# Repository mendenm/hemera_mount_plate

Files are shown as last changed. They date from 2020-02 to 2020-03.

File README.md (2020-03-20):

# Hemera Extruder Mounting Plate for Anet A8 - type printers
Designed by Marcus Mendenhall, February, 2020
## Purpose
This project is to develop an very easy-to-use, 3D printable,  adapter plate to mount an [E3D Hemera Extruder](https://e3d-online.com/e3d-hemera) on a 3d printer of the type similar to an Anet A8, Ender 3, or (probably) most Prusa I3-derived printers.

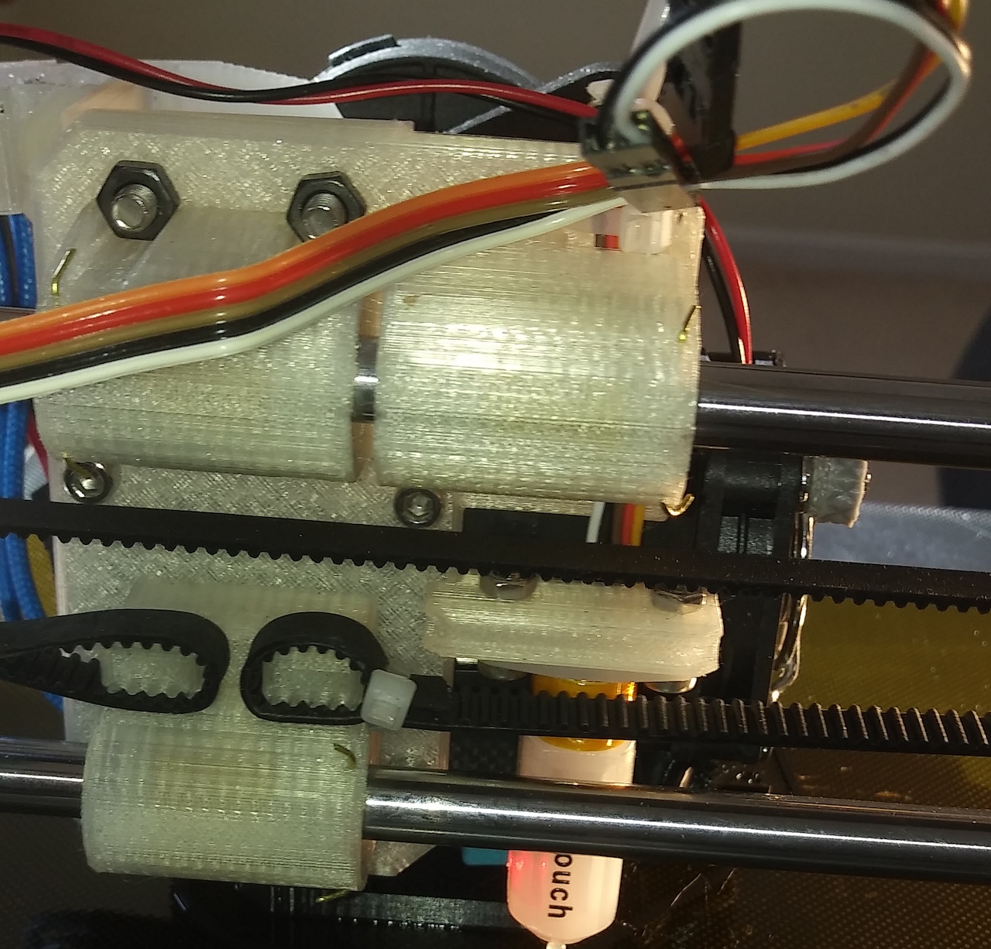
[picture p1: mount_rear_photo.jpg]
Picture of installed mount

Photograph of the back side of the mount, installed with BLTouch.

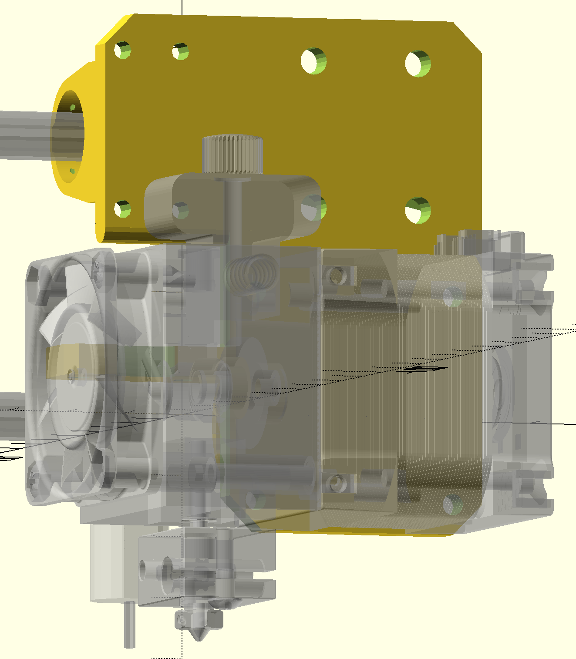
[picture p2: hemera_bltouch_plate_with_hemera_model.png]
Front view of model

Model of the plate in OpenScad showing Hemera and BLTuch ghosted in.  From front.

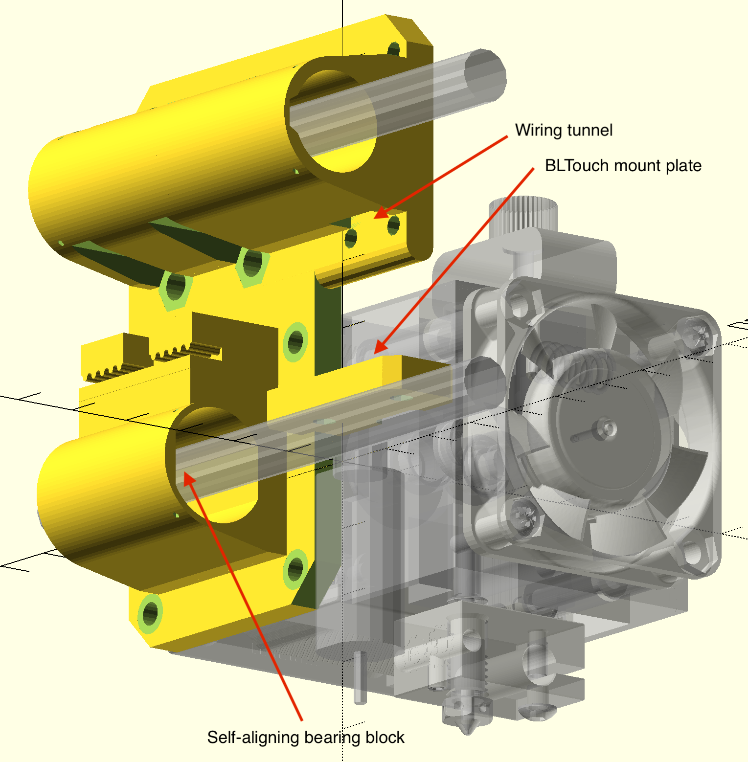
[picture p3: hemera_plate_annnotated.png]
Annotated model view

Annotated image showing some of the features

## Features

The design of plate incorporates a number of critical features. 

1.  The bearing mounting blocks are printed directly onto the plate, greatly reducing the number of screws required to assemble, and the weight.
1. The bottom bearing block is self-aligning.  The design makes it fairly insensitive to the spacing between the guides rods on the printer, and also fairly robust against inaccuracies in the printing itself.  Any rod spacing between 45 mm and 48 mm should work without even modifying the design. This is particularly useful for high-quality, close-fitting bearings such as Igus Drylin, which have little tolerance for misalignment.
1. The design is in [OpenSCAD](https://www.openscad.org), making it very easy to customize.  It is set up with OpenSCAD Customizer-compatible parameters at the top, making simple changes to the design as easy as filling in a dialog box.
1. The plate has an integrated mount for a  [BLTouch bed sensor](https://www.antclabs.com), tightly fit between the Hemera and the guide rods, putting it only 25 mm from the nozzle, with zero x offset.

## Build and use notes
* You can get the Hemera STL from <https://e3d-online.dozuki.com/c/Hemera_CAD> which will appear as a 'ghost' when OpenSCAD visualizes the mount. 
* The tiny holes in the bearing blocks are for brass wire to retain the bearings.  This is a lot easier to use than *#$&^%@ snap rings.
* The "Nozzle High" customizer setting is the one I prefer.  It mounts the Hemera fairly high and well in between the guide rods.  The other setting has it squarely straddling the lower bearing block.
* The square tunnel under the left-hand (looking from the front) bearing block is so that the wiring harness from a BLTouch can pass neatly under.  It has a pair of holes on each side of the tunnel for cable ties to strain-relieve the wiring.
* The screw hole pattern on the right-hand bearing block, which matches the pattern a normal, detached bearing block would have, is for affixing extra items to the frot of the plate.  I use the upper row to attach my cable chain. Note that in the "Nozzle high" position, the lower row of holes is nearly useless, since it is partly covered by the drive motor on the Hemera.
* The odd 'bump' in the bore of the two upper bearing blocks is to keep the seam from the final closure of the bridge from impacting the quality of the bore. 
* The flats on the top and bottom of the bottom bearing block bore is what permits the self-alignment.  These flats allow the bottom bearing some freedom of movement in the direction between the two guide rods, while keeping the bering tightly confined in the perpendicular direction.  
* I printed the one I am currently using with plain PLA, and it works fine.  The Hemera drive motor barely gets warm at 1 amp drive current.  I am printing a second one using an HTPLA, which is probably optimal;  PLA is very rigid and strong, and this plate should be stiff.  If you have a heated enclosure, you probably want HTPLA, but might use ABS instead, which will be slightly flexible. I haven't tried any exotic, very-high-temperature materials.
 
## Status Updates
* As of Feb. 21, 2020, I have been printing using this mount on my printer.   It took about 3 hours from opening the Hemera box until I got my first print.  
* 2020-02-23 Moved screw holes on BLTouch mount out 1 mm to eliminate a collision between the power connector on the BLTouch and the Hemera body.  With them in their previous position, the BLTouch was slightly angled because of this collision. It works fine, nonetheless.
* 2020-02-24 Working on actually documenting the project so it is useful on GitHub
* There are some pictures on Facebook at <https://www.facebook.com/groups/1068531466501015/permalink/2880642818623195/>.  You (unfortunately) have to be a member of the group to see these, so you may have to register.

## License
 [CC BY-NC-SA 4.0](https://creativecommons.org/licenses/by-nc-sa/4.0/)
Non-commercial sharing permitted with attribution.

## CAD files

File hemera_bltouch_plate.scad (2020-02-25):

inch=25.4+0; // make it an equation to shiwld from customizer

// distance between rods on x-axis
x_rod_spacing=46; 

// distance between centers of top double bearing
bearing_axial_separation=30;

// thickness of back plate
main_plate_thickness=5; // [3:1:10]

// diameter of x guide rods
rod_dia=8.0;

// outside diameter of linear bearing
nominal_bearing_dia=15.0; 

// Length of actual linear bearing
bearing_length=24;  

// print clearance to make bearing fit
bearing_clearance = 0.2; // [0:0.01:0.4]

bearing_dia=nominal_bearing_dia+bearing_clearance; 

// distance of bearing centerline above back plate
bearing_centerline_height=13; 

rod_clearance_dia=rod_dia+2; // room inside bearing housings, wire half spacing

// thickness of bearing outer wall
bearing_sleeve_thickness=2.0; // [1:0.1:4]

bearing_base_thickness=bearing_centerline_height-nominal_bearing_dia/2-2;

// extra length of bearing block over nominal bearing length
bearing_overhang=5.0;

bearing_base_width_1=nominal_bearing_dia+2*bearing_sleeve_thickness+4;
bearing_base_width_2=bearing_base_width_1;

// diameter of hole for wire to keep bearing in block
bearing_retainer_wire_dia=1.0;
bearing_retainer_wire_spacing=bearing_length+bearing_retainer_wire_dia;
bearing_block_total_length=bearing_retainer_wire_spacing+bearing_overhang;

// altitude of lower bearing, probably always zero
lower_bearing_z=0;

// distance between belt holder and bottom rail
belt_offset_from_bottom_rail=17.9;

// from hemera manual
hemera_bottom_screw_to_nozzle=24.2; 
// altitude of bottom screw holes on hemera
hemera_bottom_screw_z=-14;

hemera_nozzle_z=hemera_bottom_screw_z-hemera_bottom_screw_to_nozzle;

// global_rotate sets whether 'z' is up for design, or 'y' is up for printing on its back
global_rotate_x=0; // [0:"world", 90:"printing"]
global_rotate=[global_rotate_x,0,0];

module chamferedBox(shape, depth=1.0, xy=true, yz=true, zx=true)
{
    xw= shape[0]; yw=shape[1]; zw=shape[2];
    l1=sqrt(2)*((xw+yw)/2 - depth);
    l2=sqrt(2)*((xw+zw)/2 - depth);
    l3=sqrt(2)*((yw+zw)/2 - depth);
    
intersection() {
        cube(shape, center=true);
        if(xy) rotate([0,0,45]) 
            cube([l1,l1, zw+2], center=true);
        if(yz) rotate([45,0,0]) 
            cube([xw+2,l3, l3], center=true);
        if(zx) rotate([0,45,0]) 
            cube([l2, yw+2, l2], center=true);
    }    
}


module bearing_screw_pattern(include_hex=false) {
    screw_hole_long_spacing=18;
    screw_hole_transverse_spacing=24;
    screw_hole_dia=4.5; // m4 screw clearance
    screw_head_across_flats=7.2; // m4 hex nut is 7 mm
    for(x=[-1/2,1/2], y=[-1/2, 1/2]) 
        translate([x*screw_hole_long_spacing,
            0, y*screw_hole_transverse_spacing]) 
        rotate([90,0,0]) {
            translate([0,0,-0.1]) cylinder(d=screw_hole_dia, h=20, $fn=20);
            if(include_hex) translate([0,0,-19.99]) 
                cylinder(d=screw_head_across_flats/cos(30), 
                    h=20, $fn=6);
        }
}


// a bltouch2 smart with the top at [0,0,0] 
// and the pin bottom at the trigger height
module bltouch2(nozzle_z) {
    bltouch_flange_top_to_nozzle=44; // trigger height recommended from manual
    bltouch_flange_top_z=nozzle_z+bltouch_flange_top_to_nozzle;
    bltouch_thickness=0.45*inch;
    bltouch_centerline=0; 
    bltouch_magnet_ring_height=7.7; //from manual, a  little less
    bltouch_flange_thickness=2.3; // from manual
    bltouch_flange_bottom_offset=bltouch_flange_top_z-bltouch_flange_thickness;
    bltouch_body_length=26.3;
    bltouch_body_bottom=-(bltouch_flange_thickness+bltouch_magnet_ring_height+bltouch_body_length);
    translate([0,0,bltouch_flange_top_z]) {
    translate([0,0,-bltouch_flange_thickness]) 
    linear_extrude(height=bltouch_flange_thickness) difference() {
        hull() {
                square(11.5, center=true);
                translate([-9,0]) circle(d=8);
                translate([ 9,0]) circle(d=8);
            }
            translate([-9,0]) circle(d=3.2, $fn=20);
            translate([ 9,0]) circle(d=3.2, $fn=20);
    }
    translate([0,0,-10]) 
        cylinder(d=8, h=bltouch_magnet_ring_height);
    translate([0,0,bltouch_body_bottom]) intersection() {
        cylinder(d=13, h=bltouch_body_length);
        cube([20,11.5,100], center=true);
    }
    translate([0,0,-bltouch_flange_top_to_nozzle]) 
        cylinder(d=2, h=7.6);
}
}
    
module bltouch_mount_plate(nozzle_z)
{
  bltouch_flange_top_to_nozzle=44; // trigger height 
  translate([0,0,bltouch_flange_top_to_nozzle+nozzle_z]) {
      translate([0,(main_plate_thickness+8)/2-main_plate_thickness,2.5]) 
      difference() {
          translate([2,0,0]) 
            chamferedBox([31,main_plate_thickness+8,5], 
                depth=2, xy=true, yz=false, zx=false);
          for(dx=[-9,9]) translate([dx,1,0])
              cylinder(d=3.5,h=20,$fn=10, center=true);
          if(0) translate([0,4,0]) rotate([0,90,0])
              cylinder(d=3,h=50,$fn=10, center=true);
          translate([0,-(main_plate_thickness+8)/2,0]) chamferedBox([10,4,6],
                depth=1, xy=true, yz=false, zx=false);
      }
  }
}

module hemera_bolt_holes() {
    // the lower holes are at z=0
        for(x=[-1,1], z=[0,2]) 
        translate([17*x, 0, 17*z])
        rotate([-90,0,0]) {
            translate([0,0,-59]) cylinder(d=3.5, h=60, $fn=20);
        translate([0,0,-0.01]) cylinder(d=6, h=10, $fn=20);            
        }
}

module gt2_teeth(lwh) {
    // a block of teeth, distributed along the 'x' axis, 
    // with the block having a transverse dimension along 'y'
    // and a height along 'z'
    // with the origin in the middle of the teeth
    l=lwh[0];
    w=lwh[1];
    h=lwh[2];
    
    teeth=floor(l/2);
    translate([-l/2, -w/2, h]) 
    rotate([-90,0,0])
    linear_extrude(height=w) {
        difference() {
            union() {
                square([l,h]);
                for(i=[0:teeth-1])
                    translate([(i+0.5)*2,h])
                        circle(d=0.999, $fn=20);
            }
            for(i=[0:teeth])
                translate([i*2,h])
                    circle(d=0.999, $fn=20);
        }
    }
}

module basic_belt_anchor() {
    translate([-8, bearing_centerline_height,0]) 
        gt2_teeth([10,6,5]);
    translate([8, bearing_centerline_height, 0]) 
        gt2_teeth([10,6,5]);
    translate([0, (bearing_centerline_height-3)/2+0.2,1]) 
        cube([26, bearing_centerline_height-3+0.4, 8], 
        center=true);
    translate([0, (bearing_centerline_height+3)/2+0.2,-2.5]) 
        cube([26, bearing_centerline_height+3+0.4, 2], 
        center=true);    
}    

module belt_anchor(tunnel=false) {
    difference() {
        union() {
            basic_belt_anchor();
            translate([0,(bearing_centerline_height+3)/2+0.2,-6])
            cube([26,(bearing_centerline_height+3)+0.2, 6], center=true);
        }
        if(tunnel) translate([0,2,0]) cube([10,4, 30], center=true);
    }
}

module bearing_block_xsect(oval=0) {
    // block cross section with base center at [0,0]
    difference() {
        union() {
            hull() {
                circle(d=bearing_dia+2*bearing_sleeve_thickness, $fn=100);
                translate(
                    [0,-bearing_centerline_height+bearing_base_thickness/2]) 
                square([bearing_base_width_1,bearing_base_thickness], center=true);
            }
            translate(
                    [0,-bearing_centerline_height+bearing_base_thickness/2]) 
                square([bearing_base_width_2,bearing_base_thickness], center=true);
        }
        if(oval==0) {
            circle(d=bearing_dia, $fn=100);
            // relieve bad bridge at top of bearing for better fit
            if(1) translate([0, bearing_dia/2-2.5]) 
                 circle(d=8, $fn=6);
            else translate([0, bearing_dia/2-3]) circle(d=8, $fn=20);
        } else { // oval
            intersection() {
                rotate(30) circle(d=bearing_dia+oval, $fn=100);
                square([bearing_dia+oval, bearing_dia], center=true);
            }
        }
    }
}
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

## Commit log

2020-02-23 initial repo
    [hemera_bltouch_plate.scad]
2020-02-24 moved bltouch holes 1mm towards guide rods to avoid electrical connector collision with hemera
    [hemera_bltouch_plate.scad]
2020-02-24 ignore stl
2020-02-25 removed extra hole in BLTouch mount, added docs
    [hemera_bltouch_plate.scad]
2020-02-25 fixed links in README, slightly modified bearing block tunnel to make nicer bridge
    [hemera_bltouch_plate.scad]
